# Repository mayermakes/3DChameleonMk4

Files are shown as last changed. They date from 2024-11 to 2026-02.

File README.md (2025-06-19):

Welcome to the 3DChameleon 4 Color Changer Source Respository

Please use this as a basis for your own multi color solution, whether that be commerical or private.  The whole idea of the 3DChameleon is to bring color printing to everyone.  Use this, learn from it, improve it, share it... make 3D printing beautiful!

This project is 100% open source using the MIT Open Source license.  The original Tinkercad files are here: https://www.tinkercad.com/things/4nptaDc06M6-3dchameleon-40-current-version

Copyright 2024 William J. Steele

Permission is hereby granted, free of charge, to any person obtaining a copy of this software and associated documentation files (the “Software”), to deal in the Software without restriction, including without limitation the rights to use, copy, modify, merge, publish, distribute, sublicense, and/or sell copies of the Software, and to permit persons to whom the Software is furnished to do so, subject to the following conditions:

The above copyright notice and this permission notice shall be included in all copies or substantial portions of the Software.

THE SOFTWARE IS PROVIDED “AS IS”, WITHOUT WARRANTY OF ANY KIND, EXPRESS OR IMPLIED, INCLUDING BUT NOT LIMITED TO THE WARRANTIES OF MERCHANTABILITY, FITNESS FOR A PARTICULAR PURPOSE AND NONINFRINGEMENT. IN NO EVENT SHALL THE AUTHORS OR COPYRIGHT HOLDERS BE LIABLE FOR ANY CLAIM, DAMAGES OR OTHER LIABILITY, WHETHER IN AN ACTION OF CONTRACT, TORT OR OTHERWISE, ARISING FROM, OUT OF OR IN CONNECTION WITH THE SOFTWARE OR THE USE OR OTHER DEALINGS IN THE SOFTWARE.

3D Brookesia:
This is a derivative variant of the 3D Chameleon Mk4 electronics, made for hand assembly (some smd soldering required).
changes:
MCU changed from ATmega328 to ATtiny3226
4 Leds added to show selected tool.
pluggable Screw terminal connectors
fits Hammond 1455 Series Case
TMC2209 Stepper drivers
Diode based bootup protection for Stepper drivers
Thermistor controlled Fan to keep electronics cool when used in 3D printer enclosure.
Reverse Voltage Protection on Inputs

The mechanical parts are unchanged.

3D Brookesia Variant by Clem "mayermakes" Mayer published under the same License as the original.
The name refers to a number of tiny chameleon species (Brookesia sp.) because it runs on ATtiny 
Link to video regarding this variant: publishing Date TBD
Link to additional ressources: TBD

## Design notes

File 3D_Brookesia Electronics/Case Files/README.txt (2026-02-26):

these files are used to modify an off the shelve aluminium case:
Hamond Manufacturing:
1455N1201BU

Available at Farnell/Newark
Order Code:2361595

SVG files are meant to help with modifyiing the original aluminium parts.
Stl files are for replacing the Endplates with 3d printed pieces.
Version B has more margin for thicker plugable Screw terminals with 5.08mm pitch.

Video on the Project Blog and Files availabe on community.element14.com/presents

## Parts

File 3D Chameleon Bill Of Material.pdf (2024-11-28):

Item | Description | # Per Kit | Source Link
Razor Blade Knife | | | 1 https://www.amazon.com/gp/product/B09V4W3XNF/ref=ppx_yo_dt_b_search_asin_title?ie=UTF8&psc=1
12V 1A Power Supply | | | 1 https://www.amazon.com/gp/product/B09Z3WX485/ref=ppx_yo_dt_b_search_asin_title?ie=UTF8&psc=1
Cables | Flip R/G Wires | | 2 Come With Motors (May need to swap center two connectors depending on manufacturer)
Motors | | | 2 NEMA 17 38-42 (Creality Style Stepper Motors)
White Tubing Bundles | | | 1 https://www.amazon.com/gp/product/B07PV8754Z/ref=ppx_yo_dt_b_search_asin_title?ie=UTF8&psc=1
Large Bearings 6800ZZ | | | 2 https://www.amazon.com/gp/product/B07FVYGD3M/ref=ppx_yo_dt_b_search_asin_title?ie=UTF8&psc=1
Large Zipties | 8" | | 6 https://www.amazon.com/gp/product/B0786QPNBM/ref=ppx_yo_dt_b_search_asin_title?ie=UTF8&psc=1
Small Zipties | 4" | | 6 https://www.amazon.com/gp/product/B07VPTXY66/ref=ppx_yo_dt_b_search_asin_title?ie=UTF8&psc=1
Black PTFE Connectors | | | 6 See White Tubing Bundles
PETG Printed Part Set | Rectangle | | 1 https://www.printables.com/model/354998-3dchameleon-mk4-upgrade-parts-with-ptfe-grip
Limit Switch | | | 1 https://www.amazon.com/gp/product/B07TWKH7F7/ref=ppx_yo_dt_b_search_asin_title?ie=UTF8&psc=1
Small T Nut (M4 20) | M4 | | 1 https://www.amazon.com/HELIFOUNER-Pieces-2020-Aluminum-Profile/dp/B0B1LTL6M5
Small T Nut (M3 20) | M3 | | 2 https://www.amazon.com/gp/product/B07SDFCTD4/ref=ppx_yo_dt_b_search_asin_title?ie=UTF8&psc=1
Silver Hex Socket Screw | M3, 0.5x35mm | | 4 https://www.amazon.com/gp/product/B07CKB2H71/ref=ppx_yo_dt_b_search_asin_title?ie=UTF8&psc=1
Black Hex Socket Screw | M3, 0.5x30mm | | 8 https://www.amazon.com/gp/product/B07NSWS9MM/ref=ppx_yo_dt_b_search_asin_title?ie=UTF8&psc=1
Mk8 Drive Gears | | | 2 https://www.amazon.com/dp/B07Z2V6V4D
Button Socket Screw | M4, 0.7x(10/8/12)mm | 1 https://www.amazon.com/gp/product/B07C9MYR2S/ref=ppx_yo_dt_b_search_asin_title?ie=UTF8&psc=1
Socket Cap Screw | M3, 0.5x10mm (was 12mm) | 2 https://www.amazon.com/gp/product/B078GP1Z7P/ref=ppx_yo_dt_b_search_asin_title?ie=UTF8&psc=1
Tiny Screws | M2.5 x 6mm Pan Head | 2 https://www.amazon.com/gp/product/B01L7PDGXO/ref=ppx_yo_dt_b_search_asin_title?ie=UTF8&psc=1
Electronics | | | 1 https://github.com/Real3DChameleon/3DChameleon
Small Bearings 625ZZ | | | 4 https://www.amazon.com/gp/product/B08F5J2R6M/ref=ppx_yo_dt_b_search_asin_title?ie=UTF8&psc=1
Springs | | | 4 https://www.amazon.com/gp/product/B07BNNHF9K/ref=ppx_yo_dt_b_search_asin_title?ie=UTF8&psc=1
4 Filament Splitter | Green Plastic | | 2 https://github.com/Real3DChameleon/3DChameleon
Screws | 2.6 x 12mm | 6

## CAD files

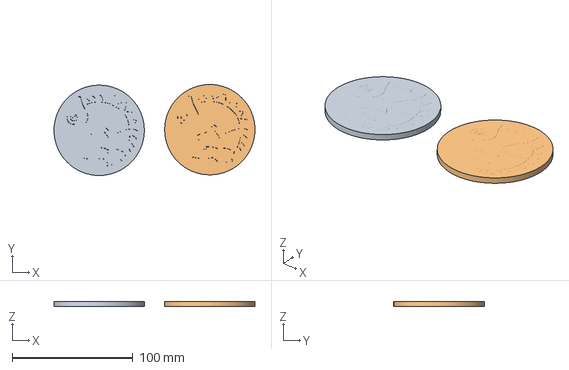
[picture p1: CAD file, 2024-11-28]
3D Chameleon Profiles/3DChameleonBambuX1C8ColorTestConfig.3mf
166.8 x 75.5 x 4.14 mm
Assembly x 2

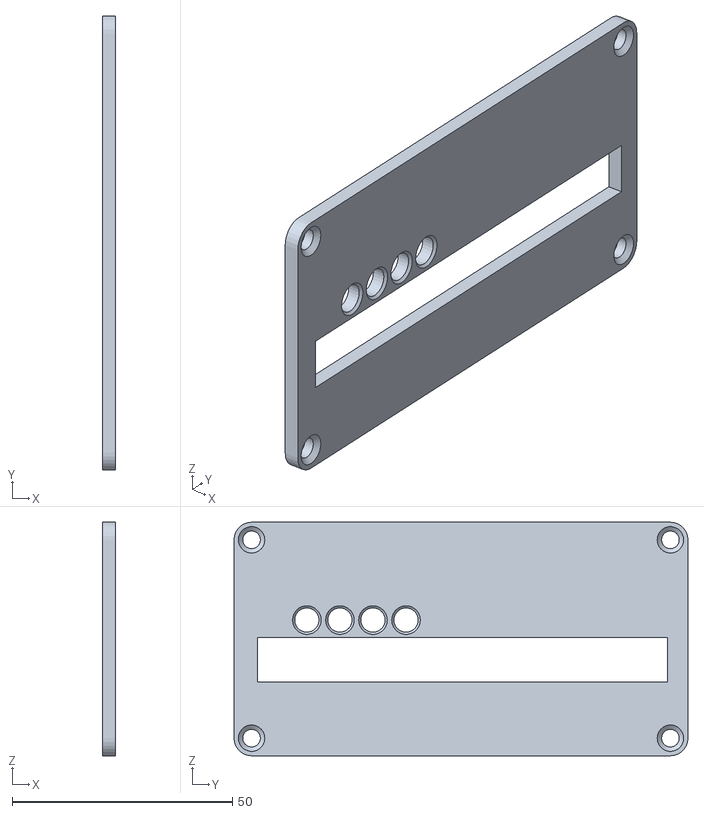
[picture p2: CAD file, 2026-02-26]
3D_Brookesia Electronics/Case Files/FrontplateB.stl
3.00 x 103.0 x 53.0

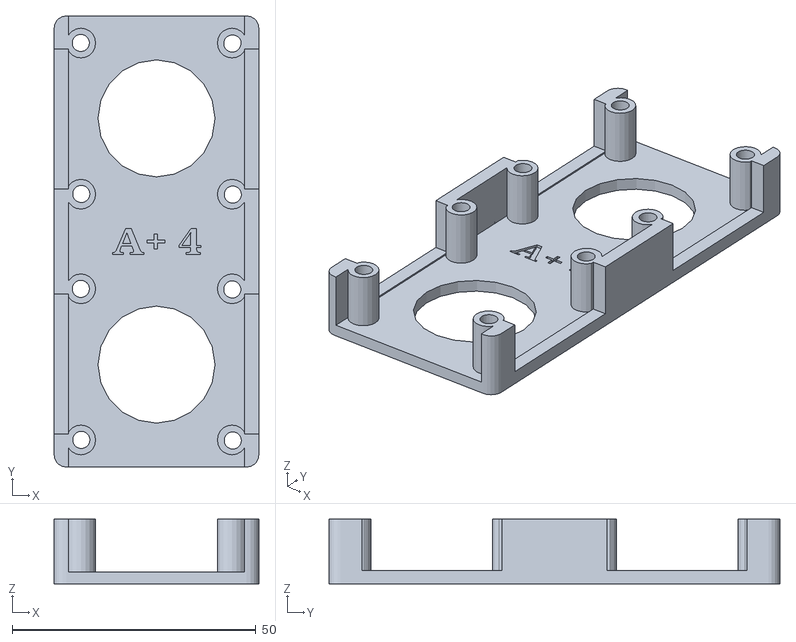
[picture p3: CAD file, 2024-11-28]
3DChameleon 4.0 (A Part).stl
42.0 x 92.5 x 13.2

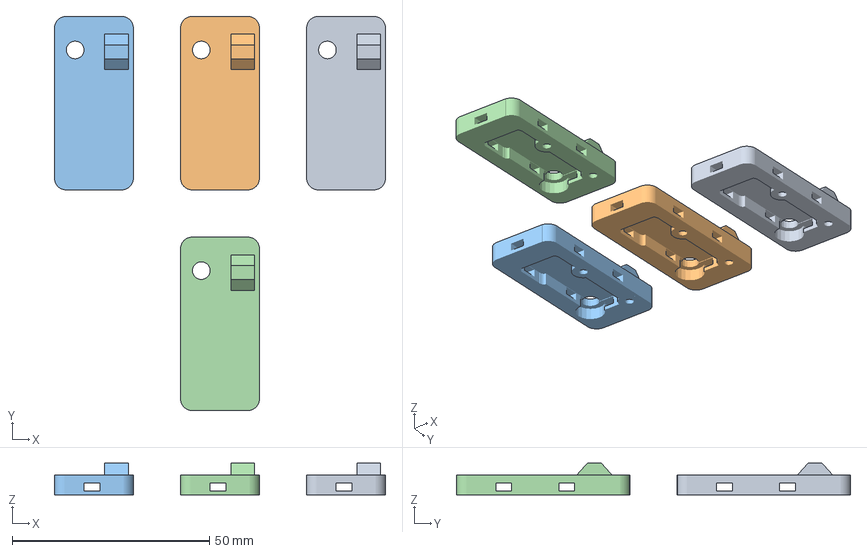
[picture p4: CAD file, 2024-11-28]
3D Chameleon Profiles/FlashforgeAdventurer5M3DChameleonProfile.3mf
84.0 x 100.0 x 8.00 mm
3DChameleon 4.0 Misc Parts.stl_4 x 4

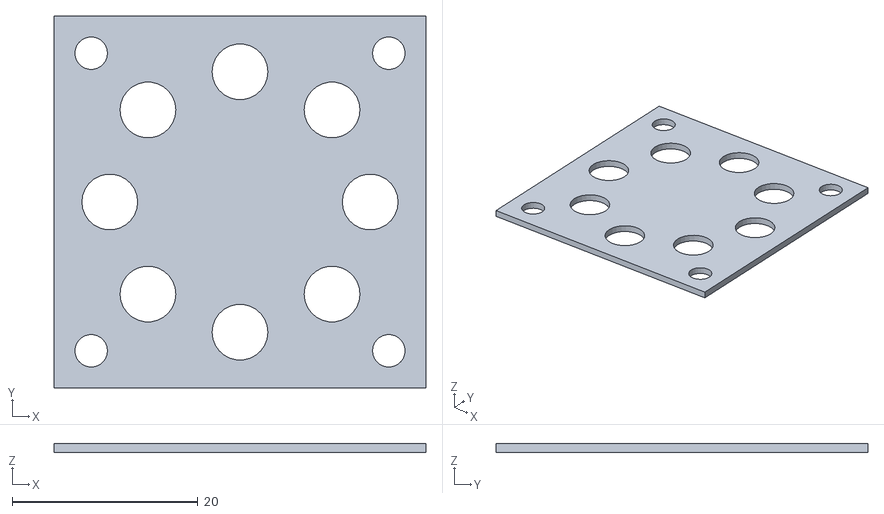
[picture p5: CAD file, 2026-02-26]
3D_Brookesia Electronics/Case Files/drillpattern.stl
40.0 x 40.0 x 1.00

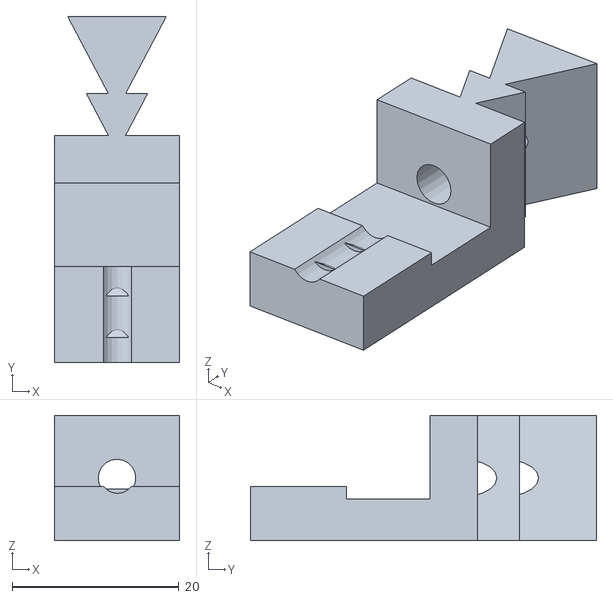
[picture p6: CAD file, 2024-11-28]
3DChameleon 4.0 (PTFE Template).stl
15.0 x 41.5 x 15.0

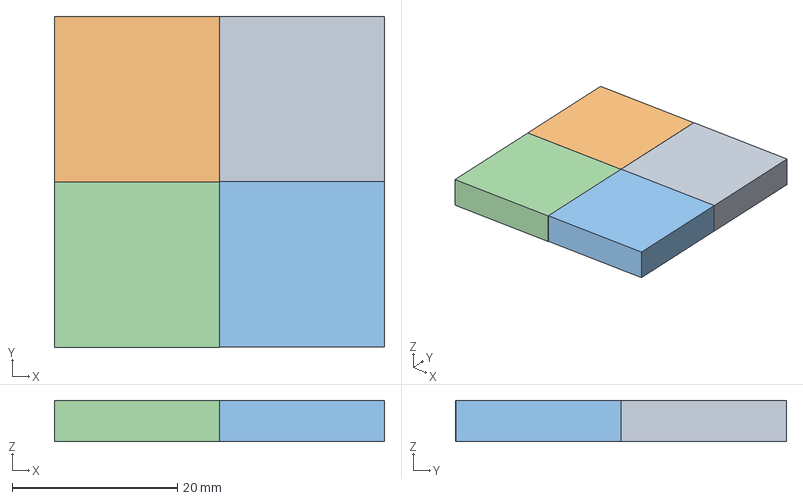
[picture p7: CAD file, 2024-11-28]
3D Chameleon Profiles/3DChameleon_BambuA1_Profile.3mf
40.0 x 40.1 x 5.00 mm

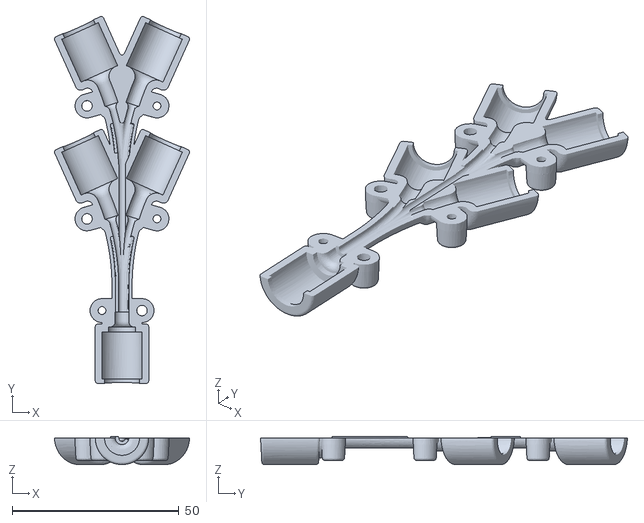
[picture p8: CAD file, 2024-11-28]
3DChameleon4YAdapter.stl
40.5 x 110.1 x 8.52

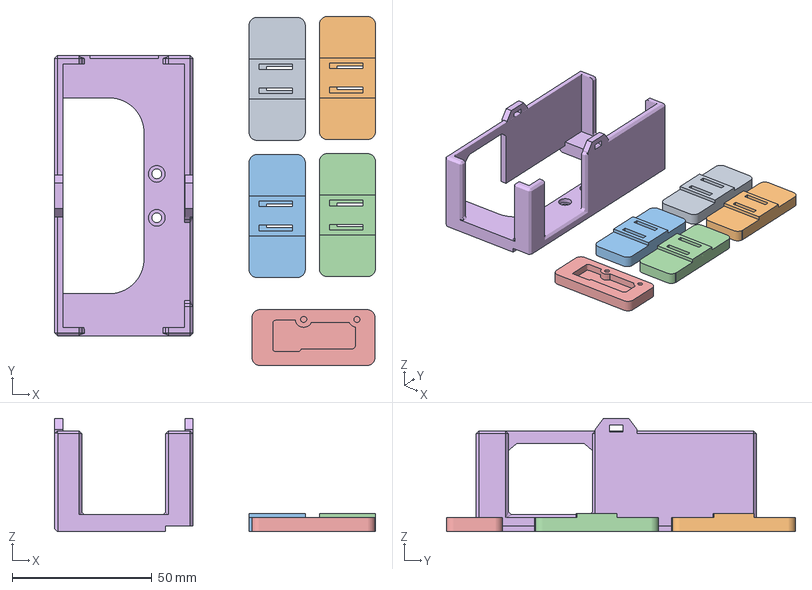
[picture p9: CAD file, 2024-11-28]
3D Chameleon Profiles/3DChameleon_Mk3_Mode3_MagnetoX_OrcaSlicer_Profile.3mf
114.7 x 124.8 x 40.4 mm
3DChameleon_MagnetoX_Wire_Mount.stl x 4
3DChameleon_MagnetoX_Switch_Mount.stl
3DChameleon_MagnetoX_Main_Mount.stl_4

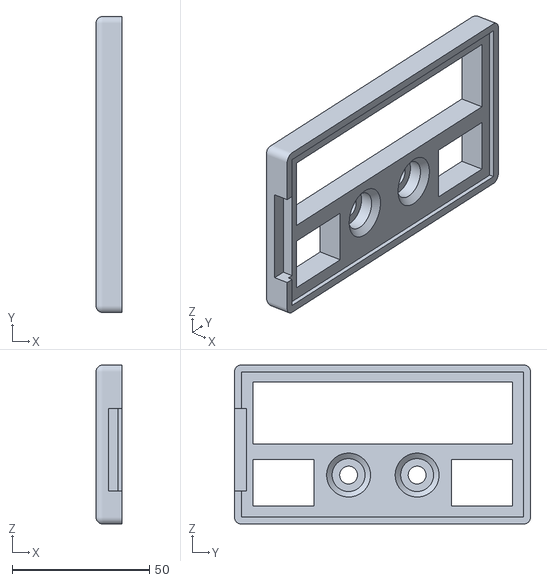
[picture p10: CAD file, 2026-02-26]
3D_Brookesia Electronics/Case Files/holder.stl
9.50 x 108.0 x 58.0

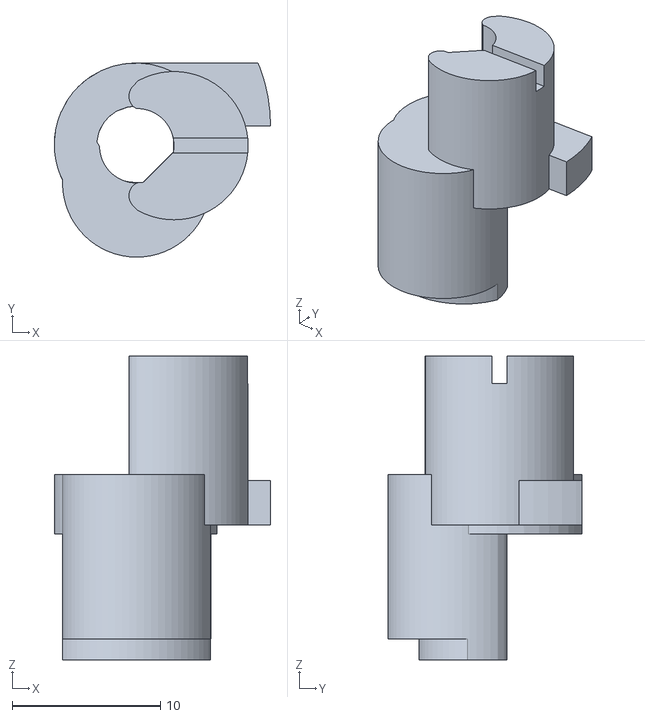
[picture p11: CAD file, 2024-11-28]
3DChameleon 4.0 (Cam).stl
14.6 x 13.1 x 20.5

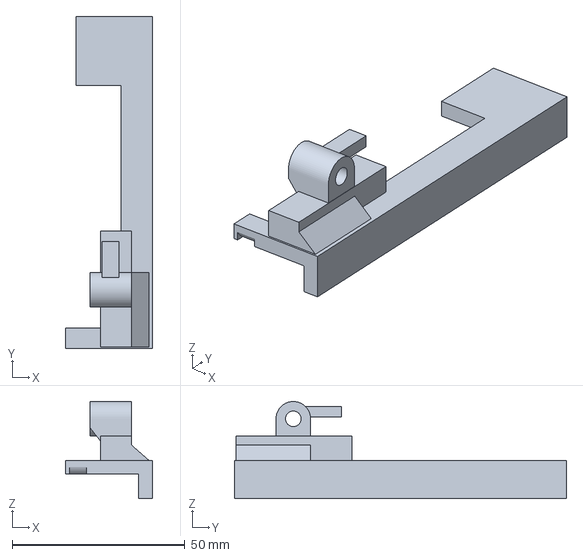
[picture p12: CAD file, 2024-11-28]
3D Chameleon Profiles/3DClippy_SovolSV06.3mf
25.1 x 96.0 x 28.1 mm

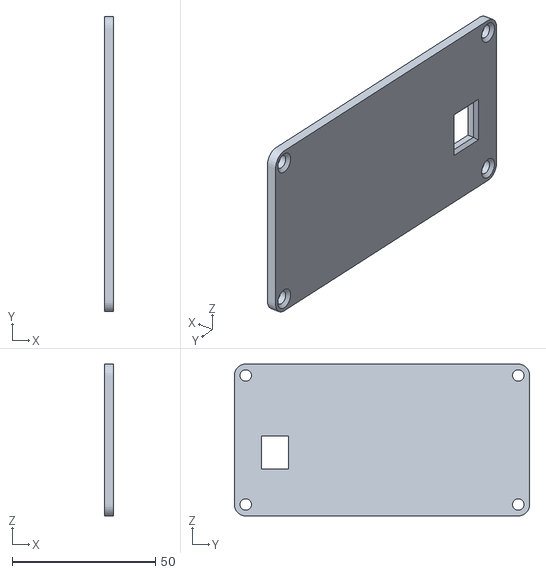
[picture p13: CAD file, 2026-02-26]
3D_Brookesia Electronics/Case Files/Backplate.stl
3.00 x 103.0 x 53.0

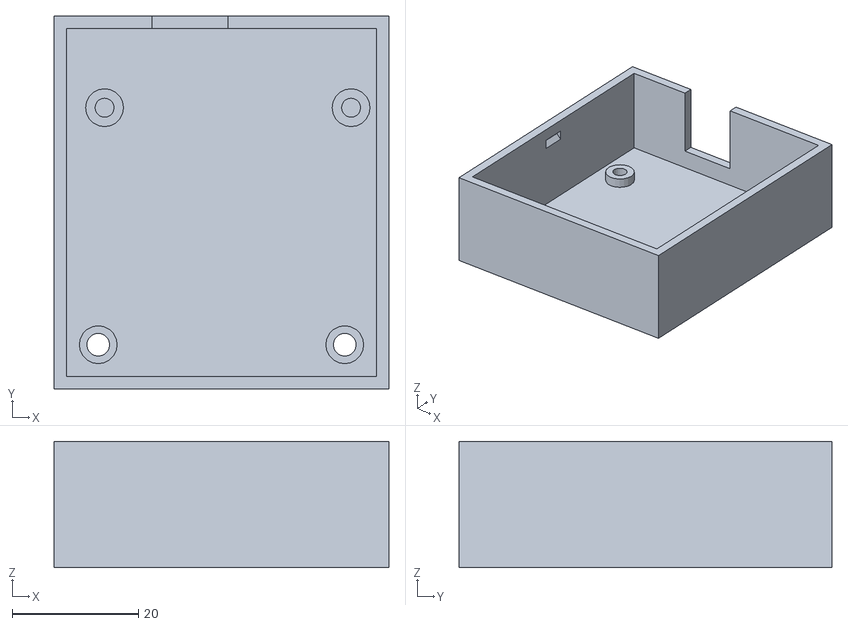
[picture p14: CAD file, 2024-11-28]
3DChameleon 4.0 (Electronics Enclosure).stl
53.0 x 59.0 x 20.0

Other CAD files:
3D_Brookesia Electronics/Case Files/Frontplate.stl
3D Chameleon Profiles/Adventurer3_3DChameleon_Profile.3mf
3DChameleon 4.0 (Electronics Lid).stl
3D Chameleon Profiles/3DChameleon_Sovol_SV-06_3DClippy_Profile (Mode 3).3mf
3D Chameleon Profiles/3DChameleon MK4 Profile For Sovol SV-08.3mf
3D Chameleon Profiles/3DChameleon Profile For Original Prusa MK4.3mf
3D Chameleon Profiles/3DChameleonBambuConfig.3mf
3D Chameleon Profiles/3DChameleonBambuConfig.gcode.3mf
3D Chameleon Profiles/3DChameleonBambuP1PTestConfig.3mf
3D Chameleon Profiles/3DChameleonCoasterPrusaMiniWithMk2.3mf
3D Chameleon Profiles/3DChameleonMk3_PrusaMk3_Mode3.3mf
3D Chameleon Profiles/3DChameleon_Bambu_A1_Mini_Profile.3mf
3D Chameleon Profiles/3DChameleon_Creality_K1.3mf
3D Chameleon Profiles/3DChameleon_Creality_K1_MAX.3mf
3D Chameleon Profiles/3DChameleon_Ender3_3DClippy_Profile.3mf
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

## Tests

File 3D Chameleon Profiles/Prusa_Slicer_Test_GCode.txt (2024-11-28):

; - 3D Chameleon Tool{next_extruder} -

;begin switch from extruder {previous_extruder} to extruder #{next_extruder}
M117 Unloading Tool [previous_extruder]

G91 ; set motion to relative

;----------- EDIT THE COMMAND BELOW ---------------

G0 X90 Y215 F5000

; this is the holding position for all future motions 
; it is the point 3mm short of the button press
; and is the only location you need to edit to tell
; the system wehre your button is.

; note: place the axis your button on 3mm short of the press
;       place the axis your button is not on in the middle
;       of the build plate.  example button is on Y axis
;       the X axis is placed in the middle at 90

;--------------------------------------------------

M82 ; turn absolute distances for the extruder

; unload extruder {previous_extruder}
G92 E0

; cool (and size) in 1.8mm tube
G0 E-50 F2000 ; quickly retract the filament to shape it
G0 E-80 F600; slowly allow it to cool

G0 E1 F2000 ; blob elimination

; back to tip size
G0 E-50 F2000 ; quickly retract the filament to shape it
G0 E-80 F600; slowly allow it to cool

G0 E1 F2000 ; blob elimination
G0 E-10 F2000 ; quickly retract the filament to shape it
G0 E1 F2000 ; quickly ram the filament to shape it
G0 E-10 F2000 ; quickly retract the filament to shape it
G0 E1 F2000 ; quickly ram the filament to shape it

; back to 1.8 constriction
G0 E-50 F2000 ; quickly retract the filament to shape it
G0 E-80 F100; slowly allow it to cool

; forging in Y adapter (adjust for extruder)
G0 E-170 F2000 ; quickly retract the filament to shape it
G0 E-110 F2000 ; quickly ram the filament to shape it
G0 E-170 F2000 ; quickly retract the filament to shape it
G0 E-110 F2000 ; quickly ram the filament to shape it

; retract it back out of the Y adapter
;G92 E0
;G0 E-80 F2000; quickly retract it back out 
G92 E0
G0 E-50 F2000; quickly retract it back out 

; load extruder #{next_extruder}
M117 Loading Tool T{next_extruder}

; always reset to extruder 0
;G0 X0 Y0 F2000 ; holding pattern 1mm short
G0 X3 Y3 F300 ; press the button
G4 P1300 ; dewll for 1.3 seconds
G0 X-3 Y-3 ; back off the button
G4 S7 wait for it to happen

; press the button for each extruder (1,2,3)

{if next_extruder>0}
G0 X3 Y3 F300 ; press the button
G4 P300 ; dewll for .3 seconds
G0 X-3 Y-3 F300 ; back off the button
G4 S2; wait for it to happen
{endif}

{if next_extruder>1}
G0 X3 Y3 F300 ; press the button
G4 P300 ; dewll for .3 seconds
G0 X-3 Y-3 F300 ; back off the button
G4 S2; wait for it to happen
{endif}

{if next_extruder>2}
G0 X3 Y3 F300 ; press the button
G4 P300 ; dewll for .3 seconds
G0 X-3 Y-3 F300 ; back off the button
G4 S2 ; wait for it to happen
{endif}

; - 3DC Process Tool {next_extruder} -

; reload filament into extruder
G92 E0
G0 E60 F2000
G92 E0
G0 E60 F2000
G92 E0
G0 E50 F2000
G92 E0

G90 ; set motion to absolute

M83 ; turn relative distances for the extruder

M117 3D Chameleon Tool T{next_extruder}

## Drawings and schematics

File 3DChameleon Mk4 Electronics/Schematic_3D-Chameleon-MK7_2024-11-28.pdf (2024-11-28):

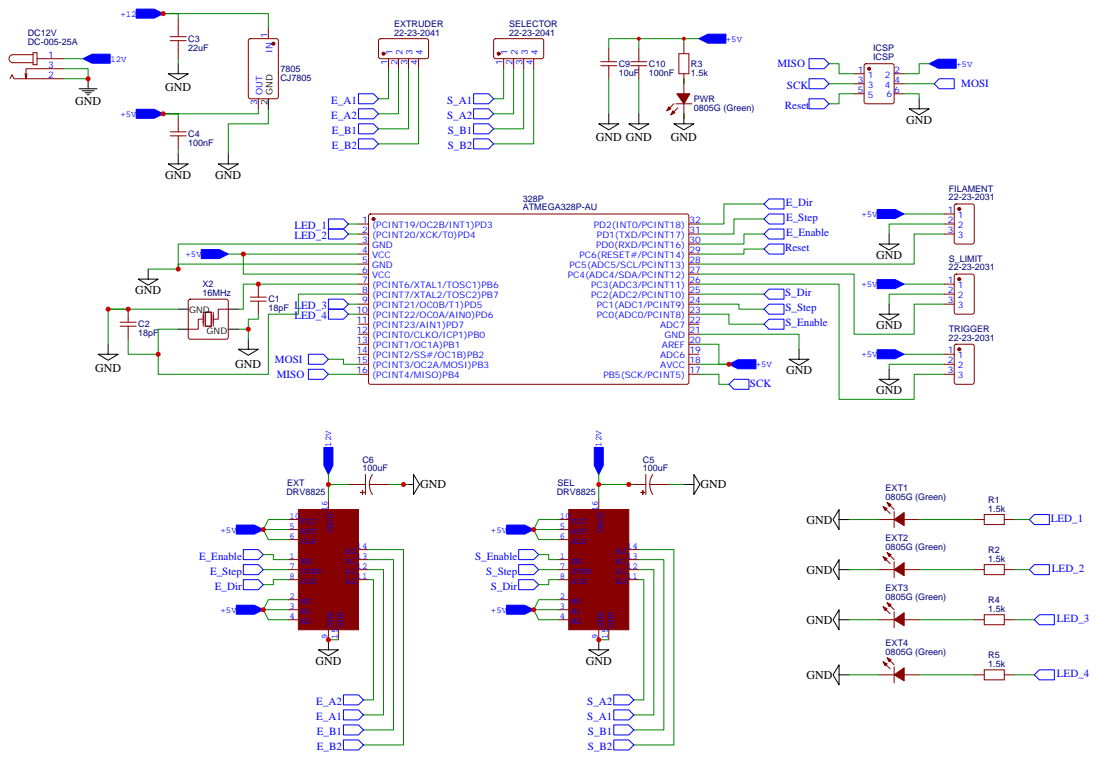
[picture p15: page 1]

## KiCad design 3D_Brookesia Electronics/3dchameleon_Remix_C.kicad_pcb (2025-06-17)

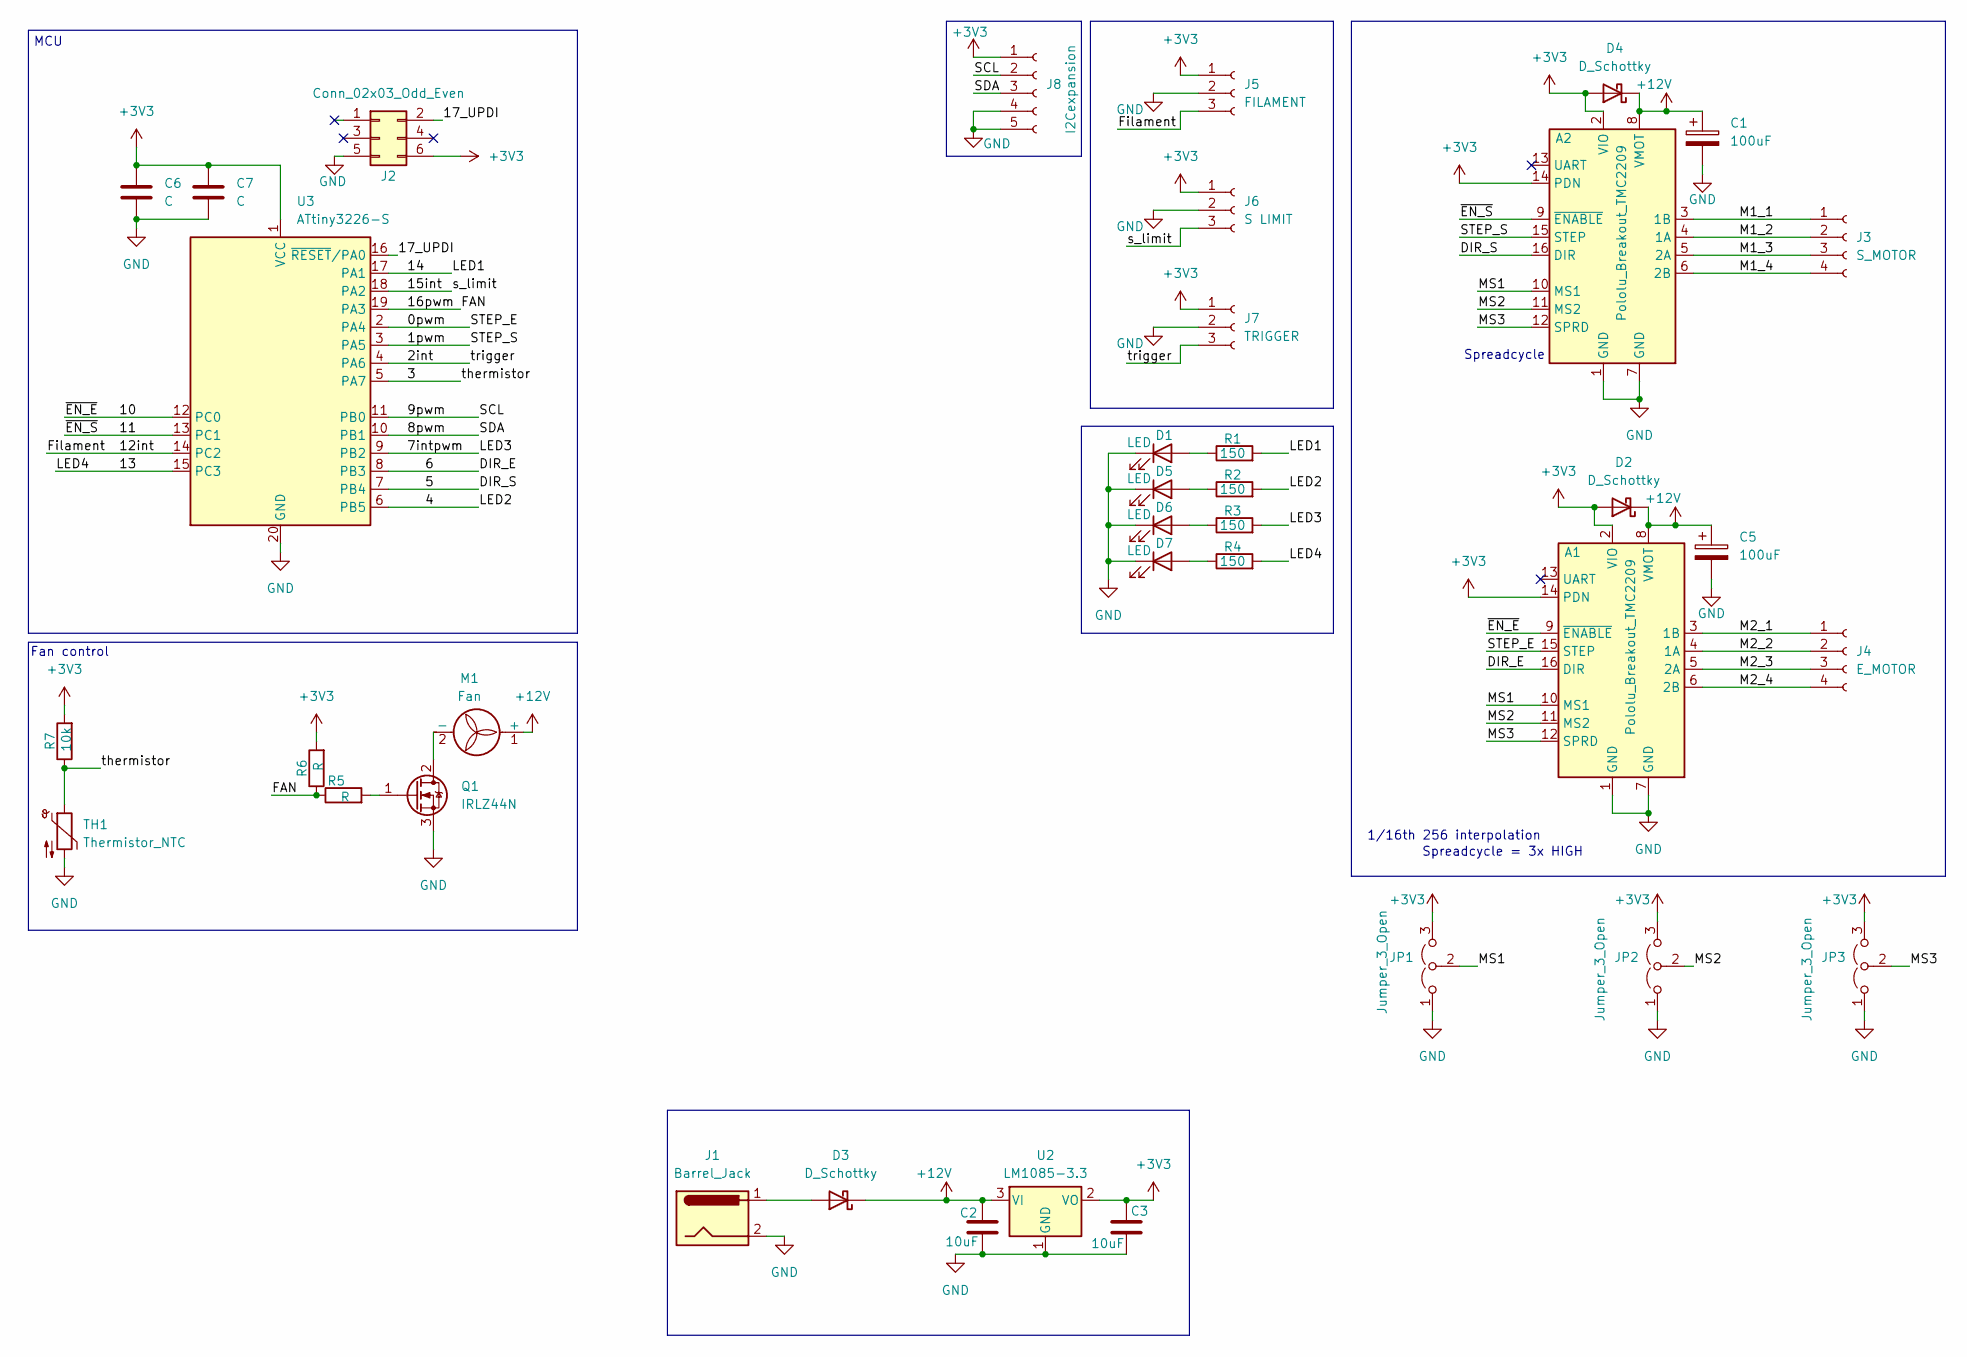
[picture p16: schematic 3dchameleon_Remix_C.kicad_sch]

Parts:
A1, A2: Pololu_Breakout_TMC2209; Pololu_Breakout-16_15.2x20.3mm
C1, C5: 100uF; CP_Radial_D10.0mm_P5.00mm
C2, C3: 10uF; C_0603_1608Metric
C6, C7: C; C_0603_1608Metric
D1, D5, D6, D7: LED; LED_D5.0mm
D2, D3, D4: D_Schottky; D_0603_1608Metric
J1: Barrel_Jack; BarrelJack_Horizontal
J2: Conn_02x03_Odd_Even; PinHeader_2x03_P2.54mm_Vertical
J3: S_MOTOR; TerminalBlock_bornier-4_P5.08mm
J4: E_MOTOR; TerminalBlock_bornier-4_P5.08mm
J5: FILAMENT; TerminalBlock_bornier-3_P5.08mm
J6: S LIMIT; TerminalBlock_bornier-3_P5.08mm
J7: TRIGGER; TerminalBlock_bornier-3_P5.08mm
J8: I2Cexpansion; PinHeader_1x05_P2.54mm_Vertical
JP1, JP2, JP3: Jumper_3_Open; SolderJumper-3_P1.3mm_Open_RoundedPad1.0x1.5mm
M1: Fan; PinHeader_1x02_P2.54mm_Vertical
Q1: IRLZ44N; TO-220-3_Horizontal_TabUp
R1, R2, R3, R4: 150; R_0603_1608Metric
R5, R6: R; R_0603_1608Metric
R7: 10k; R_0603_1608Metric
TH1: Thermistor_NTC; R_Axial_DIN0614_L14.3mm_D5.7mm_P5.08mm_Vertical
U2: LM1085-3.3; TO-263-3_TabPin2
U3: ATtiny3226-S; SOIC-20W_7.5x12.8mm_P1.27mm

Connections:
+3V3: A1.2 (VIO), A1.14 (PDN), A2.2 (VIO), A2.14 (PDN), C3.1, C6.1, C7.1, D2.2 (A), D4.2 (A), J2.6, J5.1, J6.1, J7.1, J8.1, JP1.3 (B), JP2.3 (B), JP3.3 (B), R6.2, R7.2, U2.2 (VO), U3.1 (VCC)
+12V: A1.8 (VMOT), A2.8 (VMOT), C1.1, C2.1, C5.1, D2.1 (K), D3.1 (K), D4.1 (K), M1.1 (+), U2.3 (VI)
/0pwm: A1.15 (STEP), U3.2 (PA4)
/1pwm: A2.15 (STEP), U3.3 (PA5)
/2int: J7.3, U3.4 (PA6)
/3: R7.1, TH1.1, U3.5 (PA7)
/4: R2.2, U3.6 (PB5)
/5: A2.16 (DIR), U3.7 (PB4)
/6: A1.16 (DIR), U3.8 (PB3)
/7intpwm: R3.2, U3.9 (PB2)
/8pwm: J8.3, U3.10 (PB1)
/9pwm: J8.2, U3.11 (PB0)
/10: A1.9 (~ENABLE), U3.12 (PC0)
/11: A2.9 (~ENABLE), U3.13 (PC1)
/12int: J5.3, U3.14 (PC2)
/13: R4.2, U3.15 (PC3)
/14: R1.2, U3.17 (PA1)
/15int: J6.3, U3.18 (PA2)
/16pwm: R5.1, R6.1, U3.19 (PA3)
/17_UPDI: J2.2, U3.16 (~RESET/PA0)
/M1_1: A2.3 (1B), J3.1
/M1_2: A2.4 (1A), J3.2
/M1_3: A2.5 (2A), J3.3
/M1_4: A2.6 (2B), J3.4
/M2_1: A1.3 (1B), J4.1
/M2_2: A1.4 (1A), J4.2
/M2_3: A1.5 (2A), J4.3
/M2_4: A1.6 (2B), J4.4
/MS1: A1.10 (MS1), A2.10 (MS1), JP1.2 (C)
/MS2: A1.11 (MS2), A2.11 (MS2), JP2.2 (C)
/MS3: A1.12 (SPRD), A2.12 (SPRD), JP3.2 (C)
GND: A1.1 (GND), A1.7 (GND), A2.1 (GND), A2.7 (GND), C1.2, C2.2, C3.2, C5.2, C6.2, C7.2, D1.1 (K), D5.1 (K), D6.1 (K), D7.1 (K), J1.2, J2.5, J5.2, J6.2, J7.2, J8.4, J8.5, JP1.1 (A), JP2.1 (A), JP3.1 (A), Q1.3 (S), TH1.2, U2.1 (GND), U3.20 (GND)
unnamed: D1.2 (A), R1.1
unnamed: D3.2 (A), J1.1
unnamed: D5.2 (A), R2.1
unnamed: D6.2 (A), R3.1
unnamed: D7.2 (A), R4.1
unnamed: M1.2 (-), Q1.2 (D)
unnamed: Q1.1 (G), R5.2

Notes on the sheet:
Fan control
Spreadcycle = 3x HIGH
MCU
Spreadcycle
1/16th 256 interpolation

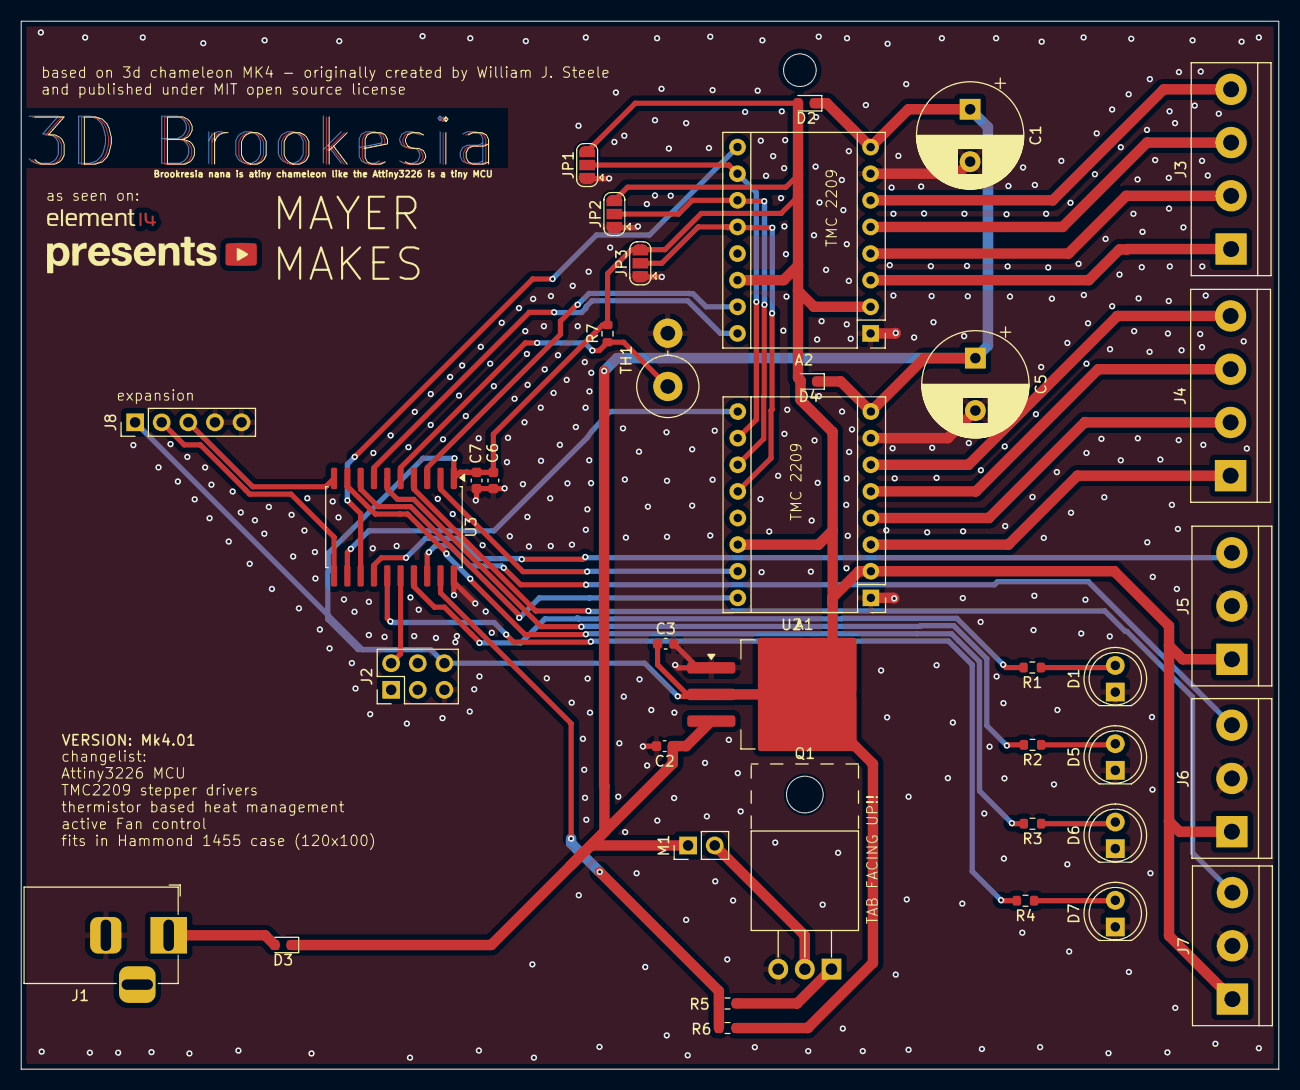
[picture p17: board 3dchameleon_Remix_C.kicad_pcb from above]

Board: 2 copper layers, 120.0 x 100.0 mm, 39 parts (0 on the bottom side), 39 nets.

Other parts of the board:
Ref**: Val**; e14presents logo 20mm silk and copper v2

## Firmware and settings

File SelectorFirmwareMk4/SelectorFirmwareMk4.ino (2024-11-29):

// November 28, 2024

/* 3DChameleon Mk4.1 Firmware

Copyright 2024 William J. Steele

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
Single Button Press Commands (count pulses of selector)

#1 - 1
#2 - 2
#3 - 3
#4 - 4
#5 - Home and Load
#6 - Unload Last and Home
#7 - Home
#8 - Next Filament
#9 - Random Filament
 
*/

#include <SSD1306Ascii.h> //i2C OLED
#include <SSD1306AsciiWire.h> //i2C OLED
#include <SparkFunSX1509.h> // sparkfun i/o expansion board - used for additional filament sensors as well as communications with secondary boards
#include <Wire.h>
#include <SPI.h>
#include <Servo.h>

#define SCREEN_WIDTH 128 // OLED display width, in pixels
#define SCREEN_HEIGHT 64 // OLED display height, in pixels

/**
 * Made with Marlin Bitmap Converter
 * https://marlinfw.org/tools/u8glib/converter.html
 *
 * This bitmap from 128x64 pasted image
 */
#pragma once

const unsigned char bitmap_logo[] PROGMEM = {
  B00000000,B00000000,B00000000,B00000000,B00000000,B00000000,B00000000,B00000000,B00000000,B00000000,B00000000,B00000000,B00000000,B00000000,B00000000,B00000000,
  B00000000,B00000000,B00000000,B00000000,B00000000,B00000000,B00000000,B00000000,B00000000,B00000000,B00000000,B00000000,B00000000,B00000000,B00000000,B00000000,
  B00000000,B00000000,B00000000,B00000000,B00000000,B00000000,B00000000,B00000000,B00000000,B00000000,B00000000,B00000000,B00000000,B00000000,B00000000,B00000000,
  B00000000,B00000000,B00000000,B00000000,B00000000,B00000000,B00000000,B00000000,B00000000,B00000000,B00000000,B00000000,B00000000,B00000000,B00000000,B00000000,
  B00000000,B00000000,B00000000,B00000000,B00000000,B00000000,B00000000,B00001000,B00000000,B00000000,B00000000,B00000000,B00000000,B00000000,B00000000,B00000000,
  B00000000,B00000000,B00000000,B00000000,B00000000,B00000000,B00110000,B00001100,B00100000,B00000000,B00000000,B00000000,B00000000,B00000000,B00000000,B00000000,
  B00000000,B00000000,B00000000,B00000000,B00000000,B00000000,B01111100,B00001110,B00110000,B00011100,B00000000,B00000000,B00000000,B00000000,B00000000,B00000000,
  B00000000,B00000000,B00000000,B00000000,B00000000,B00000000,B01111111,B00011111,B01111000,B00011111,B00000000,B00000000,B00000000,B00000000,B00000000,B00000000,
  B00000000,B00000000,B00000000,B00000000,B00000000,B00000000,B01111111,B10011111,B11111000,B00011111,B10000000,B00000000,B00000000,B00000000,B00000000,B00000000,
  B00000000,B00000000,B00000000,B00000000,B00000000,B00000000,B01111111,B11011111,B11110110,B00011111,B11000000,B00000000,B00000000,B00000000,B00000000,B00000000,
  B00000000,B00000000,B00000000,B00000000,B00000000,B00000000,B01111111,B10000000,B00000110,B00011111,B11100000,B00000000,B00000000,B00000000,B00000000,B00000000,
  B00000000,B00000000,B00000000,B00000000,B00000000,B11111100,B01111101,B11111111,B11110010,B00111111,B11110000,B00000000,B00000000,B00000000,B00000000,B00000000,
  B00000000,B00000000,B00000000,B00000000,B00000000,B11111111,B00001111,B11111111,B11111110,B00111111,B11111000,B00000000,B00000000,B00000000,B00000000,B00000000,
  B00000000,B00000000,B00000000,B00000000,B00000000,B01111111,B00111111,B11111111,B11111111,B00111111,B11111100,B00000000,B00000000,B00000000,B00000000,B00000000,
  B00000000,B00000000,B00000000,B00000000,B00000000,B01111110,B00111111,B11111111,B11111111,B01111111,B11111100,B00000000,B00000000,B00000000,B00000000,B00000000,
  B00000000,B00000000,B00000000,B00000000,B00000000,B01111101,B11111111,B11111111,B11111111,B01111111,B11111110,B00000000,B00000000,B00000000,B00000000,B00000000,
  B00000000,B00000000,B00000000,B00000000,B00000000,B01111011,B11111111,B11111111,B11111110,B11111111,B11111110,B00000000,B00000000,B00000000,B00000000,B00000000,
  B00000000,B00000000,B00000000,B00000000,B00000000,B01100111,B11101111,B11111111,B11111111,B11111111,B11111110,B00000000,B00000000,B00000000,B00000000,B00000000,
  B00000000,B00000000,B00000000,B00000000,B00000111,B10001111,B11110111,B11111111,B11111111,B11111111,B11111111,B00000000,B00000000,B00000000,B00000000,B00000000,
  B00000000,B00000000,B00000000,B00000000,B00001111,B10111111,B11111011,B11111111,B11111101,B11111110,B00011111,B00000000,B00000000,B00000000,B00000000,B00000000,
  B00000000,B00000000,B00000000,B00000000,B00001111,B10111111,B11111001,B11111111,B11111111,B11111100,B00001111,B00000000,B00000000,B00000000,B00000000,B00000000,
  B00000000,B00000000,B00000000,B00000000,B00001111,B01111111,B11111101,B11111111,B11111111,B11111001,B11110111,B00000000,B00000000,B00000000,B00000000,B00000000,
  B00000000,B00000000,B00000000,B00000000,B00000111,B11111111,B11111110,B11111111,B11111111,B11111011,B11110011,B00000000,B00000000,B00000000,B00000000,B00000000,
  B00000000,B00000000,B00000000,B00000000,B00000010,B11111111,B11111110,B11111111,B11111111,B11111011,B10111011,B00000000,B00000000,B00000000,B00000000,B00000000,
  B00000000,B00000000,B00000000,B00000000,B00111100,B11111111,B11111111,B01111111,B11111111,B11111011,B11110011,B00000000,B00000000,B00000000,B00000000,B00000000,
  B00000000,B00000000,B00000000,B00000000,B01111101,B11111111,B11111111,B01111111,B11111111,B11111001,B11110111,B00000000,B00000000,B00000000,B00000000,B00000000,
  B00000000,B00000000,B00000000,B00000000,B01111101,B11111111,B11111111,B10111111,B11111101,B11111100,B11101111,B00000000,B00000000,B00000000,B00000000,B00000000,
  B00000000,B00000000,B00000000,B00000000,B00111101,B11111111,B11111111,B10000000,B00000000,B11111111,B11011111,B00000000,B00000000,B00000000,B00000000,B00000000,
  B00000000,B00000000,B00000000,B00000000,B00011001,B11111111,B11111111,B10000000,B00000000,B11111111,B11111111,B00000000,B00000000,B00000000,B00000000,B00000000,
  B00000000,B00000000,B00000000,B00000000,B00001011,B11111111,B11111111,B01100000,B00000000,B01111111,B11111111,B00000000,B00000000,B00000000,B00000000,B00000000,
  B00000000,B00000000,B00000000,B00000000,B00000001,B11111111,B11111110,B11111000,B00000000,B00111111,B11111111,B00000000,B00000000,B00000000,B00000000,B00000000,
  B00000000,B00000000,B00000000,B00000000,B00011010,B01111111,B11111101,B11111110,B00000000,B00001111,B11111110,B00000000,B00000000,B00000000,B00000000,B00000000,
  B00000000,B00000000,B00000000,B00000000,B01111011,B11100111,B11111011,B11111110,B00000000,B00000111,B11111110,B00000000,B00000000,B00000000,B00000000,B00000000,
  B00000000,B00000000,B00000000,B00000000,B11111011,B11111100,B01110000,B01111111,B00000000,B00000001,B11111110,B00000000,B00000000,B00000000,B00000000,B00000000,
  B00000000,B00000000,B00000000,B00000000,B01111011,B11111111,B00000000,B01111111,B10000000,B00000000,B01111100,B00000000,B00000000,B00000000,B00000000,B00000000,
  B00000000,B00000000,B00000000,B00000000,B00011011,B11111111,B11000000,B11111111,B11111000,B00000000,B00000000,B00000000,B00000000,B00000000,B00000000,B00000000,
  B00000000,B00000000,B00000000,B00000000,B00001011,B11111111,B11100001,B11111111,B11111110,B00000000,B00000000,B00000000,B00000000,B00000000,B00000000,B00000000,
  B00000000,B00000000,B00000000,B00000000,B00111011,B11111111,B11100001,B11111111,B11111111,B00000000,B00000000,B00000000,B00000000,B00000000,B00000000,B00000000,
  B00000000,B00000000,B00000000,B00000000,B01111011,B11111111,B11100011,B11111111,B11110011,B10000000,B00000000,B00000000,B00000000,B00000000,B00000000,B00000000,
  B00000000,B00000000,B00000000,B00000000,B11111011,B11111111,B11100000,B00000001,B11111100,B00000000,B00000000,B00000000,B00000000,B00000000,B00000000,B00000000,
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
};


// Declaration for an SSD1306 display connected to I2C (SDA, SCL pins)
#define OLED_RESET  -1 // Reset pin # (or -1 if sharing Arduino reset pin)
#define OLED_I2C_ADDRESS 0x3C
SSD1306AsciiWire oled;

// define sparkfun io expansion
const byte SX1509_ADDRESS = 0x3E; // SX1509 I2C address
#define SX1509_FILAMENT_0 0
#define SX1509_FILAMENT_1 1
#define SX1509_FILAMENT_2 2
#define SX1509_FILAMENT_3 3
#define SX1509_OUTPUT 4
SX1509 io;                        // Create an SX1509 object to be used throughout


// defines pins numbers - 3D Chameleon Board
#define extEnable 0
#define extStep 1
#define extDir 2

#define selEnable A0
#define selStep A1
#define selDir A2

#define trigger A3
#define s_limit A4
#define filament A5

const int counterclockwise = HIGH;
const int clockwise = !counterclockwise;

const int stepsPerRev = 200;
const int microSteps = 16;
const int speedDelay = 170;

const int defaultBackoff = 10;

Servo filamentCutter;  // create servo object to control a servo
int cutterPos = 0;    // variable to store the servo position
bool reverseServo = true;

int currentExtruder = -1;
int nextExtruder = 0;
int lastExtruder = -1;
int tempExtruder = -1;

int seenCommand = 0;
int prevCommand = 0;

int loaderMode = 2;  //(0= direct drive, 1=loader/unloader, 2=loader/unloader with press)

long triggerTime = 300;
long pulseTime = (triggerTime / 2);

long distance = 10;

long unloadDistance = stepsPerRev * microSteps * distance;  // this is 10 revs - about 10"
long loadDistance   = unloadDistance * 1.1;           // this is 11 revs - about 11"

int address = 0;
byte value;

long idleCount = 0;
bool logoActive = false;
bool T0Loaded = false;
bool T1Loaded = false;
bool T2Loaded = false;
bool T3Loaded = false;


bool displayEnabled = false;
bool ioEnabled = false;
//int sensorEnabled = 0;

long randomNumber = 0;

void setup()
{

  Wire.begin(); //start i2C  
	Wire.setClock(400000L); //set clock

  // set up IO expander
  if (io.begin(SX1509_ADDRESS) == true)
  {
    io.pinMode(SX1509_FILAMENT_0, INPUT_PULLUP);
    io.pinMode(SX1509_FILAMENT_1, INPUT_PULLUP);
    io.pinMode(SX1509_FILAMENT_2, INPUT_PULLUP);
    io.pinMode(SX1509_FILAMENT_3, INPUT_PULLUP);
    io.pinMode(SX1509_OUTPUT, OUTPUT);
    ioEnabled = true;
  }

  // enable OLED display
  oled.begin(&Adafruit128x64, OLED_I2C_ADDRESS);

  // wait for it to start up
  delay(50);
    

  // welcome screen
  oled.setFont(Adafruit5x7);
  oled.clear(); //clear display
	oled.println("");
  oled.println("       Welcome!"); //print a welcome message  
  oled.println("");
  oled.println("    3DChameleon Mk4"); //print a welcome message
  oled.println("");
  oled.println("         Pro");
  delay(3000);

  displayText(0, "       Ready!");
  
  seenCommand = 0;

  // Sets the two pins as Outputs
  pinMode(extEnable, OUTPUT);
  pinMode(extStep, OUTPUT);
  pinMode(extDir, OUTPUT);

  pinMode(selEnable, OUTPUT);
  pinMode(selStep, OUTPUT);
  pinMode(selDir, OUTPUT);

  // set up the button
  pinMode(trigger, INPUT_PULLUP);  // selector

  // a little override here... we're using the two inputs as I2C instead
  pinMode(s_limit, OUTPUT);    
  pinMode(filament, OUTPUT); 

  // lock the selector by energizing it
  digitalWrite(selEnable, HIGH);

  // make sure filament isn't blocked by gillotine
  connectGillotine();
  cutFilament();
  disconnectGillotine();
  
  prevCommand = 0;

}

int lastLoop = 0;

void loop()
{
  static uint32_t lastTime = 0;

  seenCommand = 0;
  idleCount++;

  // process button press
  if (digitalRead(trigger) == 0)
  {
    idleCount = 0;
    logoActive = false;
    unsigned long nextPulse;
    unsigned long pulseCount = 0;
    unsigned long commandCount = 0;

    // keep counting (and pulsing) until button is released
    while (digitalRead(trigger) == 0)
    {
      if(pulseCount<pulseTime)
      {
        pulseCount++;
        displayCommand(pulseCount);
        if(pulseCount>1) vibrateMotor();
      }
      delay(400);  // each pulse is 400+ milliseconds apart 
    }
    processCommand(pulseCount); // ok... execute whatever command was caught (by pulse count)
    pulseCount = 0;
  }

  // updates IO block, duh!  No really, grabs the state of the sparkfun gpio expansion
  updateIOBlock();

  // each loop adds 50ms delay, so that gets added AFTER the command is processed before the next one can start
  delay(50);
}

// read the sparkfun SX1509 io
void updateIOBlock()
{
    if(ioEnabled)
    {
      T0Loaded = io.digitalRead(SX1509_FILAMENT_0);
      T1Loaded = io.digitalRead(SX1509_FILAMENT_1);
      T2Loaded = io.digitalRead(SX1509_FILAMENT_2);
      T3Loaded = io.digitalRead(SX1509_FILAMENT_3);
    }
}

// display command for each button pulse
void displayCommand(long commandCount)
{

  switch(commandCount)
  {
  case 2:
    displayText(25, "    Switch to T0");
    break;
  case 3:
    displayText(25, "    Switch to T1");
    break;
  case 4:
    displayText(25, "    Switch to T2");
    break;
  case 5:
    displayText(25, "    Switch to T3");
    break;
  case 6:
    displayText(25, "    Home/Load T0");
    break;
  case 7:
    displayText(28, "    Unload/Home");
    break;
  case 8:
    displayText(50, "        Home");
    break;  
  case 9:
    displayText(50, "        Next");
    break;
  case 10:
    displayText(40, "       Random");
    break;
  default:
    displayText(30, "     No Command");
    break;
  }
}

// execute the pulse count command
void processCommand(long commandCount)
{

  // select case for commands
  switch (commandCount)
  {
  case 2: // unload current, switch to #0, load
    displayText(30, "     T0 Selected");
    currentExtruder = 0;
    processMoves();
    displayText(35, "      Idle - T0");
    break;

  case 3: // unload current, switch to #1, load
    displayText(30, "     T1 Selected");
    currentExtruder = 1;
    processMoves();
    displayText(35, "      Idle - T1");
    break;

  case 4: // unload current, switch to #3, load
    displayText(30, "     T2 Selected");
    currentExtruder = 2;
    processMoves();
    displayText(35, "      Idle - T2");
    break;

  case 5: // unload current, switch to #4, load
    displayText(30, "     T3 Selected");
    currentExtruder = 3;
    processMoves();
    displayText(35, "      Idle - T3");
    break;

  case 6: //home and reload #1
    displayText(40, "      Homing...");
    homeSelector();
    displayText(15, "   Press to Load T0");
    gotoExtruder(0, 0);
    if(loaderMode>0)rotateExtruder(clockwise, loadDistance);
    if(loaderMode>0)gotoExtruder(0, 1);
    currentExtruder = 0;
    lastExtruder = 0;
    displayText(35, "      Idle - T0");
    break;
    
  case 7: // unload current and rehome selector
    displayText(30, "     Cutting...");
    connectGillotine();
    cutFilament();
    switch(lastExtruder)
    {
      case 0:
        displayText(10, "  Press to Unload T0");
        break;
      case 1:
        displayText(10, "  Press to Unload T1");
        break;
      case 2:
        displayText(10, "  Press to Unload T2");
        break;
      case 3:
        displayText(10, "  Press to Unload T3");
        break;
    } 
    if(loaderMode>0)gotoExtruder((lastExtruder==3?2:lastExtruder+1),lastExtruder);
    if(lastExtruder<2)
    {
      if(loaderMode>0)rotateExtruder(counterclockwise, unloadDistance);
    }
    else
    {
      if(loaderMode>0)rotateExtruder(clockwise, unloadDistance);
    }
    disconnectGillotine();
    displayText(50, "        Idle");
    break;

  case 8:  
    displayText(40, "     Homing...");
    homeSelector();
    displayText(50, "        Idle");
    break;

  case 9: // move to next available filament
    displayText(30, "     Cutting...");
    connectGillotine();
    cutFilament();
    displayText(30, "     Next Tool");
    currentExtruder++;
    if(currentExtruder==4)currentExtruder=0;
    processMoves();
    displayText(35, "        Idle");
    break;

  case 10: // move to a random filament
    displayText(30, "     Cutting...");
    connectGillotine();
    cutFilament();
    displayText(30, "    Random Tool");

    // select a random number
    randomNumber = random(0,2) + 1;

    // skip ahead that many tools
    for(long i=0; i<randomNumber; i++)
    {
      currentExtruder++;
      if(currentExtruder==4)currentExtruder=0;
    }
    processMoves();
    displayText(50, "        Idle");
    break;
    
  default:
    displayText(47, "       Clear");
    delay(200);

    displayText(50, "        Idle");
    break;
  }
}

// just the routine to update the OLED
void displayText(int offset, String str)
{

  //if(displayEnabled){
    oled.clear();
    oled.println("");
    oled.println("   3DChameleon Mk4"); //print a welcome message
    oled.println("");
    oled.println("");
    oled.println(str);
    oled.println("");
    oled.println("");
    if(ioEnabled)
    {
      oled.print("     ");
      if(T0Loaded)
      {
        oled.print("0  ");
      }
      else
      {
        oled.print("+  ");
      }
      if(T1Loaded)
      {
        oled.print("1  ");
      }
      else
      {
        oled.print("+  ");
      }
      if(T2Loaded)
      {
        oled.print("2  ");
      }
      else
      {
        oled.print("+  ");
      }
      if(T3Loaded)
      {
        oled.println("3");
      }
      else
      {
        oled.println("+");
      }
    }
    else
    {
      oled.println("     -  -  -  -");
    }
  //  }
}

// real work is here
void processMoves()
{

  // make sure we have a real extruder selected
  if(lastExtruder>-1)
  {

    // if so, we need to cut the filament
    displayText(30, "     Cutting...");
    connectGillotine();
    cutFilament();

    // ok... then wait for the 2nd button press to unload it
    switch(lastExtruder)
    {
      case 0:
        displayText(10, "  Press to Unload T0");
        break;
      case 1:
        displayText(10, "  Press to Unload T1");
        break;
      case 2:
        displayText(10, "  Press to Unload T2");
        break;
      case 3:
        displayText(10, "  Press to Unload T3");
        break;
    } 

    // roll over to first if on last
    if( loaderMode>0 ) gotoExtruder( ( lastExtruder==3 ? 2 : (lastExtruder+1)), lastExtruder);

    // this determines which direction to move the motor, 0-1 : counterclockwise, 2-3 : clockwise
    if(lastExtruder<2)
    {
      if(loaderMode>0)rotateExtruder(counterclockwise, unloadDistance);
    }
    else
    {
      if(loaderMode>0)rotateExtruder(clockwise, unloadDistance);
    }
  }
  else
  {
    lastExtruder = 0;
  }
  disconnectGillotine();
  
  // tell it to actually execute that command now
  gotoExtruder(lastExtruder, currentExtruder);

  // ok... filament unloaded, time to load the new... so tell the user
  switch(currentExtruder)
  {
    case 0:
      displayText(15, "   Press to Load T0");
      break;
    case 1:
      displayText(15, "   Press to Load T1");
      break;
    case 2:
      displayText(15, "   Press to Load T2");
      break;
    case 3:
      displayText(15, "   Press to Load T3");
      break;
  }

  // same (but inversed) logic for motor direction
  if(currentExtruder<2)
  {
    if(loaderMode>0)rotateExtruder(clockwise, loadDistance);
  }
  else
  {
    if(loaderMode>0)rotateExtruder(counterclockwise, loadDistance);
  }

  // if we're loading, then load it now
  if(loaderMode>0)gotoExtruder(currentExtruder, (currentExtruder==3?2:currentExtruder+1));

  // everybody remember where we parked!
  lastExtruder = currentExtruder;
}


// this function simply moves from the currentCog to the targetCog is the best way
void gotoExtruder(int currentCog, int targetCog)
{
 
  int newCog = targetCog - currentCog;

  // ok... which way
  int newDirection = counterclockwise;
  if(newCog<0)
  {
    // we need to move the other way
    newDirection = clockwise;

    //and since we know we went too far... let's go the other way in steps as well
    newCog = currentCog - targetCog;
  }

  // if we're already on the current cog, then do nothing
  if(newCog > 0)
  {    
    // advance tool targetCog times
    for(int i=0; i<newCog; i++)
    {
      rotateSelector(newDirection, (stepsPerRev / 4) * microSteps);
    }
  }
}

// move the extruder motor in a specific direction for a specific distance (unless it's a "until button is not pressed")
void rotateExtruder(bool direction, long moveDistance)
{
  // note to bill:  make this acecelerate so it's very fast!!!
  
  digitalWrite(extEnable, LOW);  // lock the motor
  digitalWrite(extDir, direction); // Enables the motor to move in a particular direction
  const int fastSpeed = speedDelay/2; // double time

  // this is depricated right now... might bring it back in the future
  if(loaderMode==1)
  {

    // Makes 50 pulses for making one full cycle rotation
    for (long x = 0; x < (moveDistance-1); x++)
    {
      // this is how we pulse the motor to get it to step
      digitalWrite(extStep, HIGH);
      delayMicroseconds(fastSpeed);
      digitalWrite(extStep, LOW);
      delayMicroseconds(fastSpeed);
    }

  }

  if(loaderMode==2)
  {

   // keep waiting until button is pressed
   while (digitalRead(trigger) != 0)
    {
      delay(50);
    }
    
    // Move while button is pressed
    while (digitalRead(trigger) == 0)
    {

      // this is how we pulse the motor to get it to step
      digitalWrite(extStep, HIGH);
      delayMicroseconds(fastSpeed);
      digitalWrite(extStep, LOW);
      delayMicroseconds(fastSpeed);
    }
  }
  // ok, done pressing button, so make sure we're not energized (high is no, low is yes)
  digitalWrite(extEnable, HIGH);
}

// similar to extruder, but only stepping 50 (of 200) at a time
void rotateSelector(bool direction, int moveDistance)
{

  // while we are at it... can we make this faster using the magic you invented above?
  
  digitalWrite(selEnable, LOW); // lock the selector
  digitalWrite(selDir, direction); // Enables the motor to move in a particular direction

    // Makes 50 pulses for making one full cycle rotation
    for (int x = 0; x < (moveDistance-1); x++)
    {
      digitalWrite(selStep, HIGH);
      delayMicroseconds(speedDelay);
      digitalWrite(selStep, LOW);
      delayMicroseconds(speedDelay);
    }
}

// this cycles the servo between two positions
void cutFilament() {
  digitalWrite(selEnable, LOW); // disable stepper so we have power!
  if(reverseServo==false)
  {
    openGillotine();
    closeGillotine();
  }
  else
  {
    closeGillotine();
    openGillotine();
  }
  digitalWrite(selEnable, HIGH);
}

// enable the servo
void connectGillotine()
{
  filamentCutter.attach(11);
}
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

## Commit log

2024-11-28 Initial Mk4 Commit
    [3DChameleon 4.0 (2020 Mount).stl, 3DChameleon 4.0 (A Part).stl, 3DChameleon 4.0 (B Part).stl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]
2024-11-28 Mk4 Electronics, Profiles Commit
    [3DChameleon MK4 Profile For Sovol SV-08.3mf, 3DChameleon Profile For Original Prusa MK4.3mf, 3DChameleonBambuConfig.3mf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]
2025-06-17 Remix of the Electronics with modern parts.
    Code not ported yet.
    [3dchameleon_Remix_C.kicad_pcb]
2025-06-19 Firmware for 3D Brookesia variant
    Changes:
    ported to Attiny3226
    Adds 4 LEDS to show which tool is active
    Adds pwm fan control based on temperature within housing.

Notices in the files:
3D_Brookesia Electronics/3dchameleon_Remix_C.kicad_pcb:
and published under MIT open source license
